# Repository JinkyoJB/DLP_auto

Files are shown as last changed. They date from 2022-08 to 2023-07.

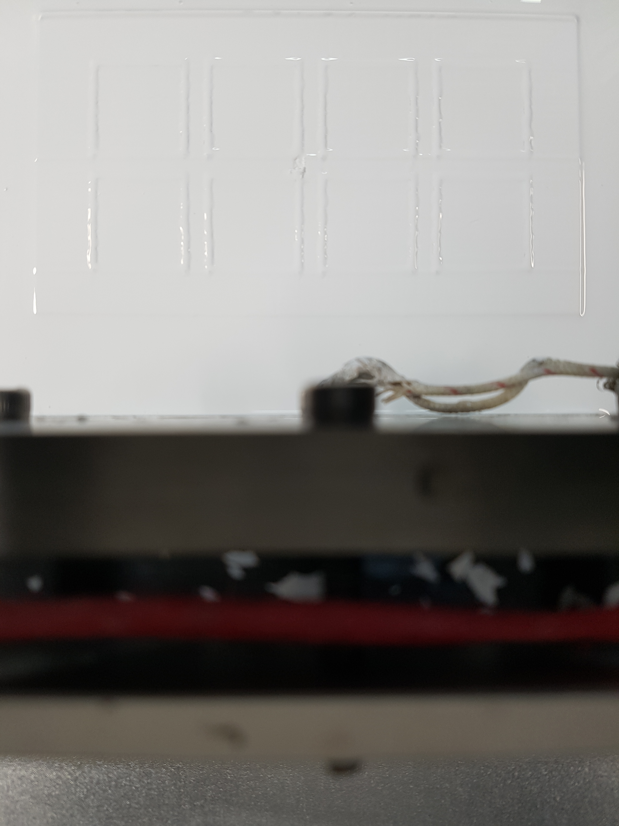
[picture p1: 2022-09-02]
DLP_GUI/DLP_temp/220808174041/20220629_163913.jpg

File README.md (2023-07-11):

# 딥러닝을 통한 DLP 3D프린터 출력 자동화

해당 내용은 서울과학기술대학교 특수정밀가공 및 생산연구실에서 진행하는 ‘ 세라믹 및 금속 재료의 3D 형상출력을 목적으로 제작된 광경화 타입 3D프린터 제작 및 딥러닝 기술을 기반으로 한 전공정 자동화 ’의 전반적인 기술 및 코드 내용입니다. 

https://user-images.githubusercontent.com/85150616/190361339-f62668f7-aa68-4073-84bd-3492f415d7a6.mp4

[제작된 3D프린터로 세라믹이 출력되는 모습]

## 1. Hardware

3D프린터의 하드웨어는 이전 연구실 연구원들이 제작한 세라믹용 광경화 3D프린터를 조금 더 개선시켜서 진행하였습니다. 자세한 규격 및 형상 정보는 ‘DLP_modeling’ 카테고리에 백업해 놓았습니다.

### 1.1. DLP_modeling

‘DLP_modeling’에서 [0.assembly-MLP_Original.prt](https://github.com/JinkyoJB/DLP_auto/blob/main/DLP_modeling/0.assembly-MLP_Original.prt) 항목은 개선시키기전 기존의 하드웨어의 데이터가 담겨있습니다. 파일형식은 ‘.prt’형식이며 NX Modeling 프로그램으로 제작되었습니다. 기존 DLP프린터 모습은 다음과 같습니다.

3D프린터-Original

[기존 3D프린터 모델링 데이터]

최종모델링
[최종 3D프린터 모델링 데이터]

[behind modeling]
  
고점도 세라믹 레진을 토출하기 위해 여러 모델링을 실험해 봤습니다.
<br>
1차적으로는 제어하기 쉬운 스텝모터를 이용해 여러 형상으로 토출을 시도해 봤으나 필요압력이 높아 구조물이 외압을 버티기 힘들어 3차 시도 끝에 공압기로 압력을 가해 토출하는 방식을 차용했습니다.

시료주사기

사용된 시료 주사기는 250ml 공업용 주사기에 3D프린터 및 o-ring으로 커스텀하여 사용하였습니다.

### 1.2. DLP_arduino
모터사양

아두이노는 시리얼 통신을 통해 말단의 모터,센서를 제어하며 컴퓨터의 GUI명령 또한 시리얼 통신으로 입력받습니다. 모터의 동작은 비동기방식이여야 하므로 일정 동작이 끝난 뒤, 아두이노는 '*'과 같은 특정 시그널을 통해 동작의 끝남을 컴퓨터에게 알리는 방식을 차용하였습니다.

### 1.3 블레이드 히팅

세라믹의 점도 및 흐름성은 온도에 반비례하는 특성을 지니므로 고점도 세라믹을 도포 시 40-70도의 블레이드가 필요합니다. 

따라서 모델링 및 가공하여 블레이드 양측에 열봉이 1개씩 삽입되고 중앙에 온도센서를 부착함으로써 히팅 블레이드를 적용했습니다.

### 1.4 flow-chart 및 diagram




---
## 2. Software

화면 캡처 2023-07-11 131624
3D프린터와 연결된 컴퓨터 화면에서는 위 이미지와 같은 화면을 볼 수 있습니다.
<br>


좌측 프로그램은 광원인 DLP 제어 프로그램이며, 중간은 3D프린터를 제어하기 위해 파이썬으로 자체 제작한 프로그램입니다. 해당 GUI를 통해 DLP에 input될 이미지, 광파워, 노광 시간, 3D프린터의 모터,센서를 조절할 수 있습니다. 또한 AI모드 출력 명령 버튼을 누르면 densenet을 적용하여 세라믹 표면에 결점이 발견 될 시 자동 재 블레이딩 및 블레이드 온도를 높이는 등의 폐루프 시스템을 적용할 수 있습니다.
맨 우측은 표면 결점을 검출하기 위해서 3D프린터 윗면에 달아둔 안드로이드기기를 통해 보여지는 이미지를 상시로 확인 할 수 있습니다. 안드로이드 연결은 파이썬을 이용해 ADB서버를 통해 통신합니다.

## 3. Deep learning

### 3.1. DLP_dataset
데이터셋은 2021.10.07~2022.02.23까지 실험 중 촬용된 세라믹 도표면 사진을 바탕으로 구성되었습니다.

정상상태(Normal)와 출력 중 빈번한 결함들로 분류했으며, 기계 자체적으로 조치를 취할 수 있는 상태인 미미한 결함(Minor defect)과 기공 상태(Pore), 적층이 아예 불가능한 심각한 상태(Critical) 및 기계오류 문제(Error) 로 총 5가지의 유형으로 분류했습니다.

### 3.2. DLP_data_augmentation
table2
데이터셋의 정확도를 높이기 위해 원본 이미지에 적절한 변형을 가해서 학습데이터셋의 규모를 인위적으로 증대하는 augmentation 기법을 적용했습니다. 각 분류의 데이터셋 양을 비슷하게 조절하고 각 가중치를 비슷하게 학습하여 정규화 및 과적합을 줄였으며, 종류는 기본적인 좌우반전, 상하반전, 랜덤위치합성 3가지를 적용했습니다. Augmentation을 적용한 최종 개수의 전체비율이 25%내외가 되도록 하여 가중치를 비슷하게 학습하도록 적용하였습니다.

이 외에도 세라믹 도표면은 광경화 반응이 일어 날 수 있도록 회백색인 경우가 많은데 이는 RGB의 값이 (255,255,255)로 편중되어 있음을 말합니다. 따라서 RGB픽셀값 표준화를 적용하여 주변 픽셀 대비 연산 픽셀의 RGB값의 변화가 더 쉽게 인식될 수 있도록 하여 학습 효율을 높였습니다. RGB평균값은 [0.485,0.456,0.406], 표준편차는 [0.229,0.224,0.225]를 적용하였으며, 적용된 최종 입력데이터의 이미지는 위 사진과 같습니다. 적용 후 보통 3%정도의 성능 향상을 확인했습니다.

### 3.3. DLP_deepLearning


준비된 데이터셋을 저명한 이미지 알고리즘에 파인 튜닝하여 적용해 본 결과, 어느정도 saturation된 결과값이 나온 것을 확인 할 수 있었습니다. 특히 denseNet에서 좋은 성능지표를 보여 해당 모델의 하이퍼파라미터를 optimization하여 3D프린터에 적용하였습니다.

---

### 결과

이렇게 폐루프 시스템으로 동작하는 세라믹 3D프린터의 출력 결과물입니다. 딥러닝을 통해 결함을 검출함으로써 sintered body에서도 정밀하고 적은 크랙을 관찰할 수 있었습니다.

### 3.4. DLP_yolo5(testing)
현재는 도포 과정이 아닌 전과정에서 일어날 수 있는 결함을 yolo5로 관측하기 위해 test 중입니다.

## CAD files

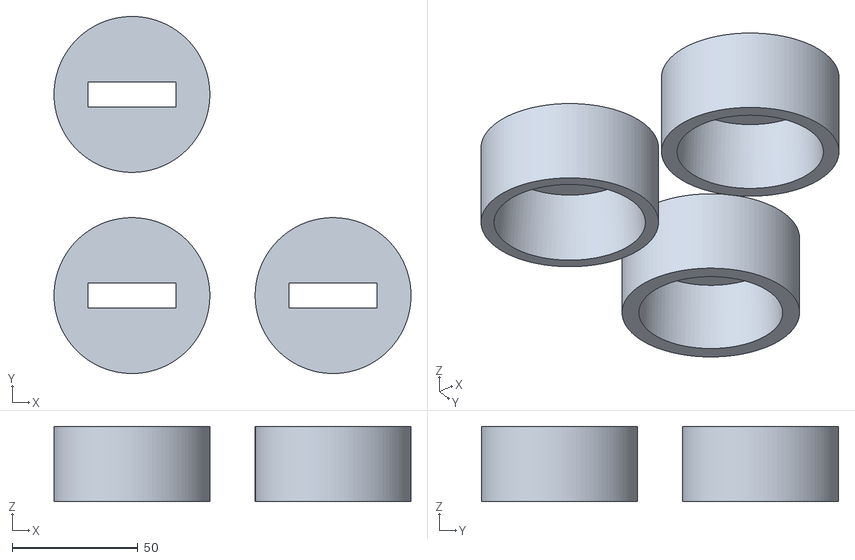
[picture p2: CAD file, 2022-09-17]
DLP_modeling/STL_files/0218_주둥이 마개.stl
142.0 x 142.0 x 30.0

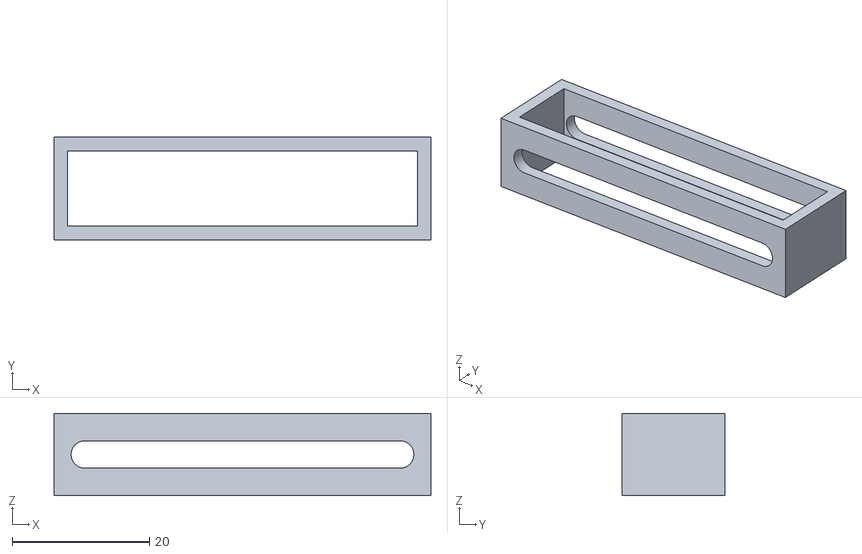
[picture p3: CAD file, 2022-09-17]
DLP_modeling/STL_files/z-limit 2.stl
55.0 x 15.0 x 12.0

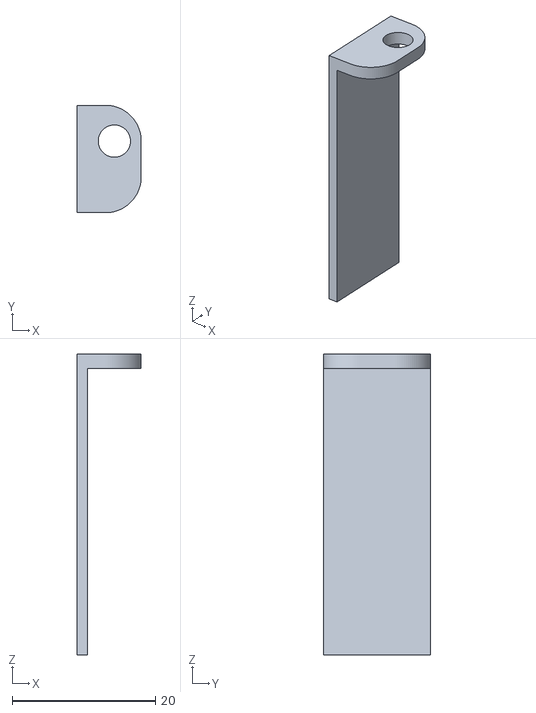
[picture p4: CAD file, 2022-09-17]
DLP_modeling/STL_files/z-limit 1.stl
9.00 x 15.0 x 42.0

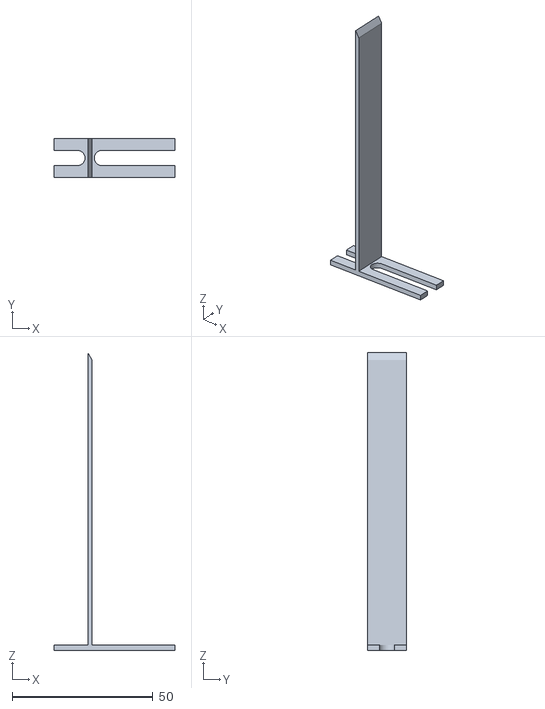
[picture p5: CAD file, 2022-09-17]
DLP_modeling/STL_files/b-limit 1.stl
43.0 x 14.0 x 106.0

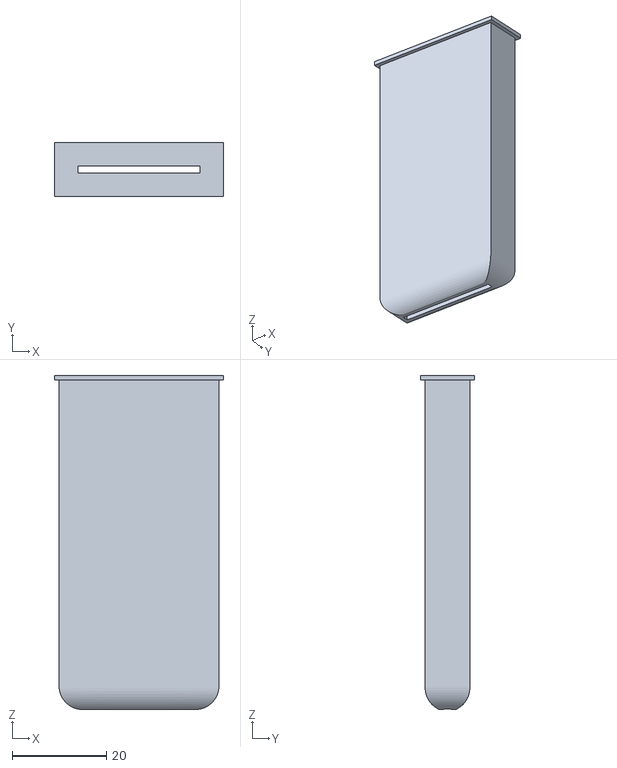
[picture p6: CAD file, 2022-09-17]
DLP_modeling/STL_files/0218_시료 주둥이.stl
36.0 x 11.5 x 71.0

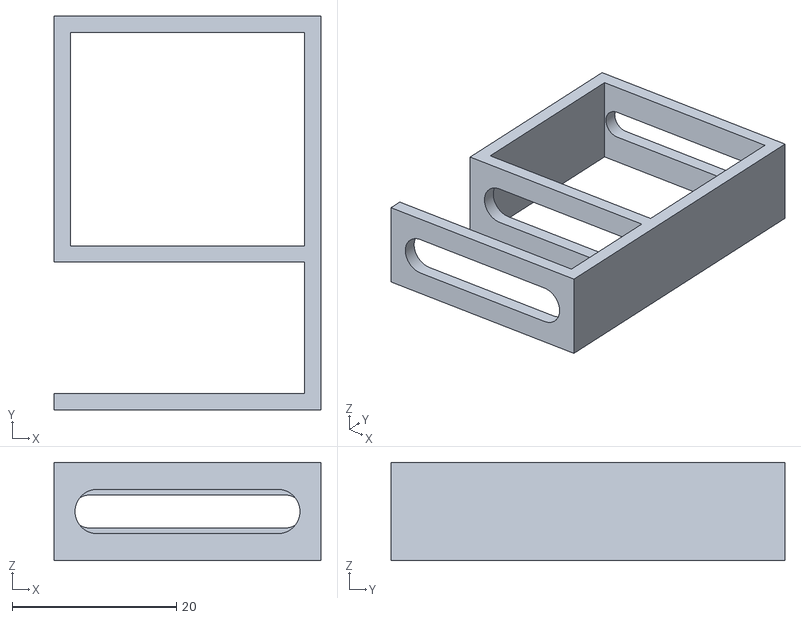
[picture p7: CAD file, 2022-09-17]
DLP_modeling/STL_files/b-limit 2.stl
32.5 x 48.0 x 12.0

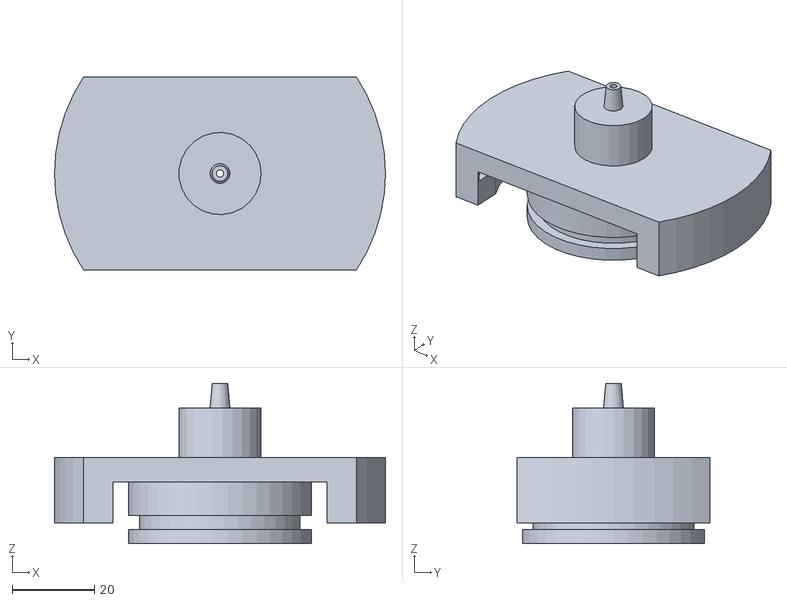
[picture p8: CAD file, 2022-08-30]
DLP_modeling/STL_files/27.air_hose.stl
80.5 x 47.0 x 39.0

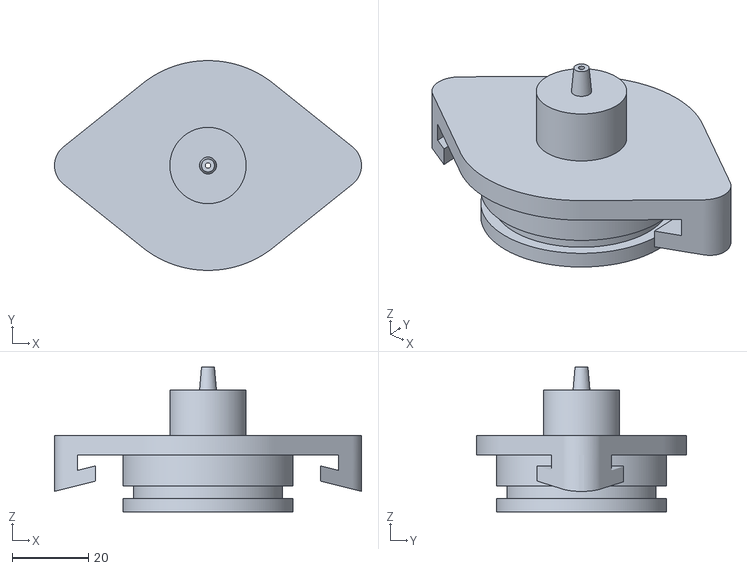
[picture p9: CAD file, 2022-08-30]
DLP_modeling/STL_files/air_hose(olde2).stl
80.5 x 55.0 x 38.0

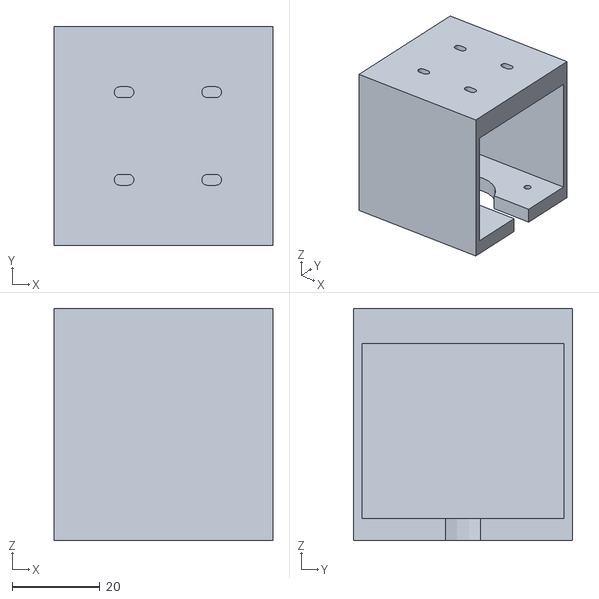
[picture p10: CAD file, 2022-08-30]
DLP_modeling/STL_files/motor-holder2.stl
50.0 x 50.0 x 53.0

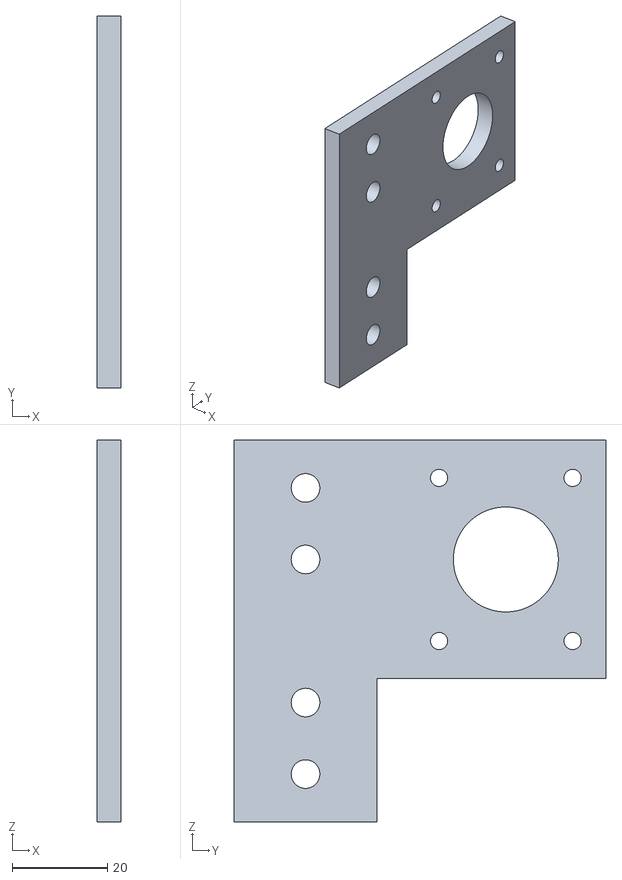
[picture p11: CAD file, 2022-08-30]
DLP_modeling/STL_files/33.motor_holer.stl
5.00 x 78.0 x 80.0

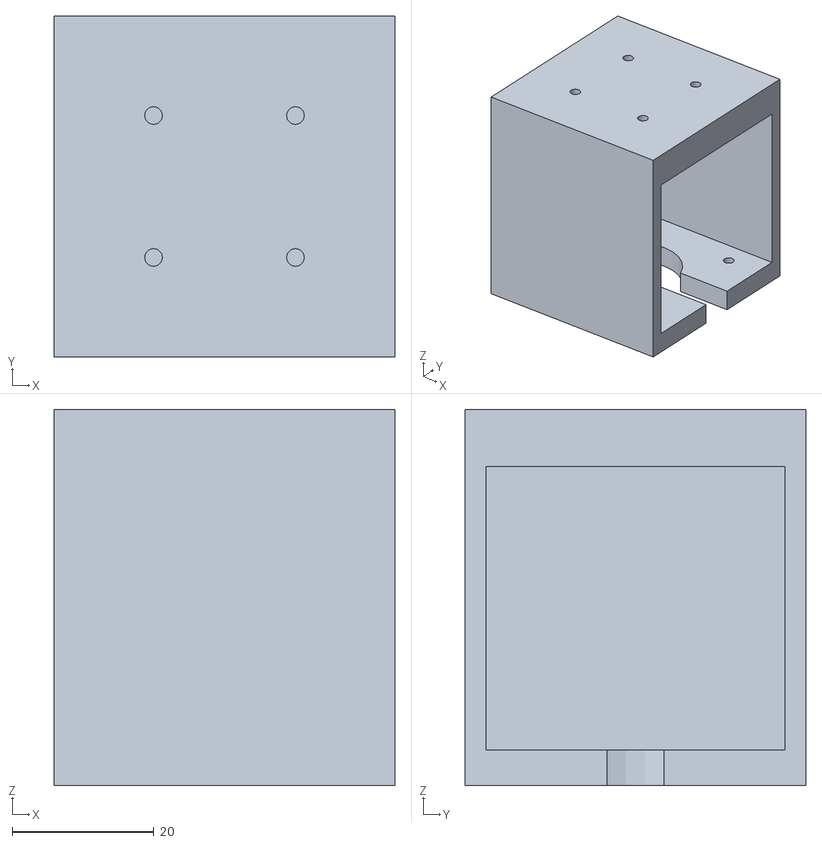
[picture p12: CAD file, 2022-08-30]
DLP_modeling/STL_files/motor-holder.stl
48.0 x 48.0 x 53.0

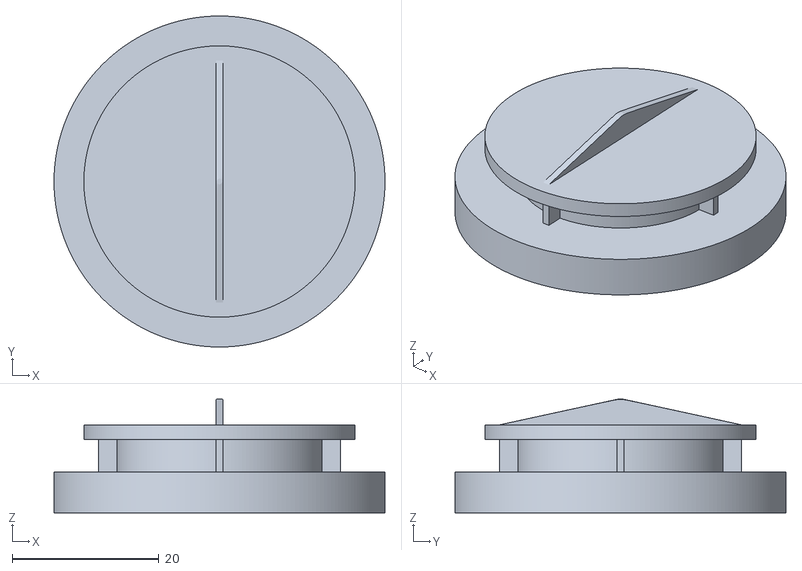
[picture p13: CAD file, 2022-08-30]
DLP_modeling/STL_files/air_cap.stl
45.2 x 45.2 x 15.5

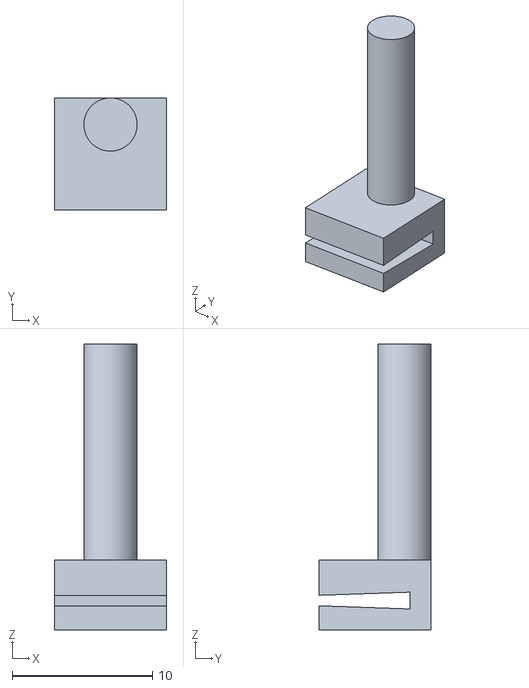
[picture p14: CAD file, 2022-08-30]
DLP_modeling/STL_files/cooling_pan_holder.stl
8.00 x 8.00 x 20.4

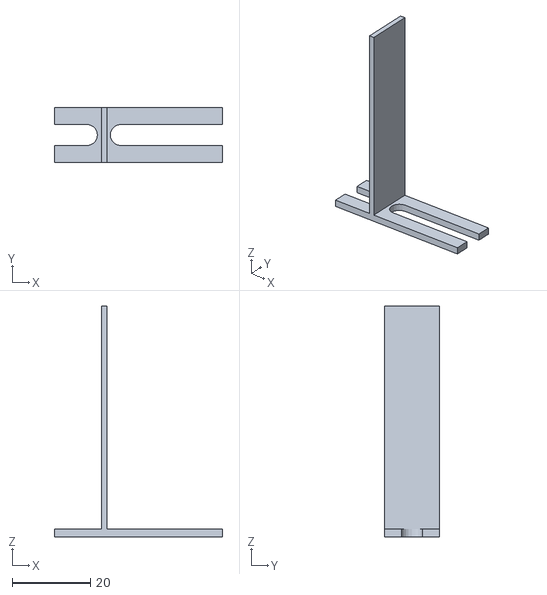
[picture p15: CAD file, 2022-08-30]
DLP_modeling/STL_files/210917 JS limitsensor-touch.stl
43.0 x 14.0 x 59.0

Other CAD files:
DLP_modeling/STL_files/211122-holder.stl
DLP_modeling/STL_files/211122-holder2.stl
DLP_modeling/STL_files/211026-2.stl
DLP_modeling/STL_files/air_hose(old).stl
DLP_modeling/0.assembly-MLP_Original.prt
DLP_modeling/00.assembly4-MLP_design.prt
DLP_modeling/1.Z-axis_frame.prt
DLP_modeling/10.ballscrew_of_gidebar.prt
DLP_modeling/11.Y_axis_acryle_part.prt
DLP_modeling/12.motor_bearing.prt
DLP_modeling/14.Y_axis_front_acrylic.prt
DLP_modeling/15.Y_axis_back_acrylic.prt
DLP_modeling/16.Y_axis_screw_bar_movement.prt
DLP_modeling/17.DLP.prt
DLP_modeling/18.Z-screw.prt
DLP_modeling/19.Z-axis_gide_bar.prt
DLP_modeling/2.X-axis_frame.prt
DLP_modeling/20.Z-axis_scew_movement..prt
DLP_modeling/21.blade_bar.prt
DLP_modeling/23.Y-axis_plate.prt
DLP_modeling/24.plate.prt
DLP_modeling/25.phone_plate.prt
DLP_modeling/27.air_hose_.prt
DLP_modeling/28.syringe_holer.prt
DLP_modeling/29.air_cap.prt
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

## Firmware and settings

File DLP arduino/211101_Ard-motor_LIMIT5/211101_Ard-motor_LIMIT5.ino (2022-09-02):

//제어용 아두이노 포트번호는 16 
//21.11.02 모터 드라이버 교체--> 이전버전 코드와 모터 방향 반대
//21.11.17 레진 모터 추가
#define Blade_DIR 53
#define Blade_STEP 51
#define Blade1_ms1 49
#define Blade1_ms2 47
#define Blade1_SP 45
#define Blade2_ms1 43
#define Blade2_ms2 41
#define Blade2_SP 39
#define Blade_e 37 //Enable

#define zaxis_DIR 52
#define zaxis_STEP 50
#define zaxis1_ms1 48
#define zaxis1_ms2 46
#define zaxis1_SP 44
#define zaxis2_ms1 42
#define zaxis2_ms2 40
#define zaxis2_SP 38
#define zaxis_e 30 //Enable

#define button 34 //0812업글
#define sensor 32 //0812업글

#define resin_SIG 2
#define Rsensor 3 
#define resin_e 4 //enable
#define resin_ms1 5
#define resin_ms2 6
#define resin_SP 7
#define resin_STEP 8
#define resin_DIR 9



void setup()
{
  pinMode(resin_e, OUTPUT);
  pinMode(Blade_e, OUTPUT);
  pinMode(zaxis_e, OUTPUT);
  digitalWrite(Blade_e,LOW);
  digitalWrite(zaxis_e,LOW);
  digitalWrite(resin_e,LOW);
  pinMode(Blade_DIR, OUTPUT);
  pinMode(Blade_STEP, OUTPUT);
  pinMode(Blade1_SP, OUTPUT);
  pinMode(Blade1_ms2, OUTPUT);
  pinMode(Blade1_ms1, OUTPUT);
  pinMode(Blade2_SP, OUTPUT);
  pinMode(Blade2_ms2, OUTPUT);
  pinMode(Blade2_ms1, OUTPUT);
 
  pinMode(resin_DIR, OUTPUT);
  pinMode(resin_STEP,OUTPUT);
  pinMode(resin_SP, OUTPUT);
  pinMode(resin_ms2, OUTPUT);
  pinMode(resin_ms1, OUTPUT);

  pinMode(zaxis_DIR, OUTPUT);
  pinMode(zaxis_STEP,OUTPUT);
  pinMode(zaxis1_SP, OUTPUT);
  pinMode(zaxis1_ms2, OUTPUT);
  pinMode(zaxis1_ms1, OUTPUT);
  pinMode(zaxis2_SP, OUTPUT);
  pinMode(zaxis2_ms2, OUTPUT);
  pinMode(zaxis2_ms1, OUTPUT);
  pinMode(resin_SIG, OUTPUT);
  
  pinMode(button, INPUT_PULLUP);
  pinMode(sensor, INPUT_PULLUP);
  pinMode(Rsensor, INPUT_PULLUP);
 
 Serial.begin(9600);
}
 
void loop()
{ 
  digitalWrite(resin_SIG,LOW);
  if(Serial.available() > 0)
  {
    String inString = Serial.readStringUntil('\n');
    int index1 = inString.indexOf(','); //문자열에 '찾을문자'가 있는 위치(index)값 반환
    int index2 = inString.indexOf(',', index1+1); //('찾을문자', 시작위치) 문자열의 시작위치에서 시작하고 '찾을문자'가 있는 위치값 반환
    int index3 = inString.length();
    int value1 = inString.substring(0, index1).toInt();
    int value2 = inString.substring(index1+1,index2).toInt();
    int value3 = inString.substring(index2+1,index3).toInt();
    
 ////Value2가 0이면 z축 관련
    if((value1 == 0) & (value2 == 0) & (value3 == 1)) /// z축이 리미트센서에 터치
    {
      zhoming();
    }
    if((value1 == 0) & (value2 == 0) & (value3 == 2)) /// z축이 블레이드 날에 닿는 위치로
    {
      zgoing();
    }

 ///value2 가 1이면 blade 관련
   if((value1 == 0) & (value2 == 1) & (value3 == 1)) ///blade Homing, 블레이드 시작 위치에서 멈추기
    {
      bhoming();
    }
   if((value1 == 0) & (value2 == 1) & (value3 == 2)) ///blade going
   {
      bgoing();
   }

   //resin함수
      if((value1 == 2) & (value2 == 2) & (value3 == 2))
   {
      resinshot();
   }
      if((value1 == 0) & (value2 == 0) & (value3 == 3)) 
    {
      Rhoming();
    }
      if((value1 == 4) & (value2 == 4) & (value3 == 4)) 
    {
      resinMS();
    }

 ///원하는 스텝만큼 모터이동하는 함수들
    if(value1 == 7) //7은 blade함수
    {
      Serial.print(" blade:"); Serial.print(value3); Serial.print("step");
      blade(value2, value3);
    }
    if(value1 == 8) //8은 zaxis함수 
    {
      Serial.print(" zaxis:"); Serial.print(value3); Serial.print("step");
      zaxis(value2, value3); 
    }
       if(value1 == 9) //9은 resin함수 
    {
      Serial.print(" resin:"); Serial.print(value3); Serial.print("step");
      resin(value2, value3); 
    }
  }
}

//blade 모터이동 2400step--6mm   1step당 0.0025mm
void blade(int direct, int step) // direct는 방향: 1은 앞으로, 0은 뒤로, step은 모터 step수,
{
    digitalWrite(Blade1_SP,LOW);
    digitalWrite(Blade1_ms2,HIGH);
    digitalWrite(Blade1_ms1,LOW);
    digitalWrite(Blade2_SP,LOW);
    digitalWrite(Blade2_ms2,HIGH);
    digitalWrite(Blade2_ms1,LOW);
  if(direct == 1)
  { 
    Serial.println(" forward");
    digitalWrite(Blade_DIR,LOW);
    for(int i = 0; i < step; i++)
      {
        digitalWrite(Blade_STEP,HIGH);
        delayMicroseconds(500);
        digitalWrite(Blade_STEP,LOW);
        delayMicroseconds(500);
      }
     Serial.println("*"); 
  }
  if(direct == 0)
  {
    Serial.println(" backward");
    digitalWrite(Blade_DIR,HIGH);
    for(int i = 0; i < step; i++)
      {
        digitalWrite(Blade_STEP,HIGH);
        delayMicroseconds(500);
        digitalWrite(Blade_STEP,LOW);
        delayMicroseconds(500);
      }
    Serial.println("*");
  }
}
//Z모터이동 3200step--4mm   1step당 0.00125mm
void zaxis(int direct, int step) // direct는 방향: 1은 앞으로, 0은 뒤로, step은 모터 step수,
{
    digitalWrite(zaxis1_SP,LOW);
    digitalWrite(zaxis1_ms2,HIGH);
    digitalWrite(zaxis1_ms1,LOW);
    digitalWrite(zaxis2_SP,LOW);
    digitalWrite(zaxis2_ms2, HIGH);
    digitalWrite(zaxis2_ms1, LOW);
  if(direct == 1)
  {
    Serial.println(" up");
    digitalWrite(zaxis_DIR,LOW);
    for(int i = 0; i < step; i++)
      {
        digitalWrite(zaxis_STEP,HIGH);
        delayMicroseconds(1000);
        digitalWrite(zaxis_STEP,LOW);
        delayMicroseconds(1000);
      }
    Serial.println("*");
  }
  if(direct == 0)
  {
    Serial.println(" down");
    digitalWrite(zaxis_DIR,HIGH);
    for(int i = 0; i < step; i++)
      {
        digitalWrite(zaxis_STEP,HIGH);
        delayMicroseconds(1000);
        digitalWrite(zaxis_STEP,LOW);
        delayMicroseconds(1000);
      }
    Serial.println("*");
  }
}
 
void bhoming()
{
  Serial.println(" homing-blade");
  digitalWrite(Blade1_SP,LOW);
  digitalWrite(Blade1_ms2,LOW);
  digitalWrite(Blade1_ms1,LOW);
  digitalWrite(Blade2_SP,LOW);
  digitalWrite(Blade2_ms2,LOW);
  digitalWrite(Blade2_ms1,LOW);
 
  digitalWrite(Blade_DIR, LOW);
  
  for(int i = 0; i < 9999999; i++ ) 
  {
    if( digitalRead(button) == HIGH) 
    {
      Serial.println(" blade touched");
      break;
    } 
    else 
    {
      digitalWrite(Blade_STEP,HIGH);
      delayMicroseconds(700);
      digitalWrite(Blade_STEP,LOW);
      delayMicroseconds(700);
    }
  }
 Serial.println("*");
}

///블레이드시작위치로 부터 일정 스텝만큼 뒤로 이동하는 함수
void bgoing()
{
    digitalWrite(Blade1_SP, LOW);
    digitalWrite(Blade1_ms2,HIGH);
    digitalWrite(Blade1_ms1,LOW);
    digitalWrite(Blade2_SP,LOW);
    digitalWrite(Blade2_ms2,HIGH);
    digitalWrite(Blade2_ms1,LOW);

    digitalWrite(Blade_DIR, HIGH);
    
  for(int i = 0; i < 32000; i++)
  {
    digitalWrite(Blade_STEP,HIGH);
    delayMicroseconds(500);
    digitalWrite(Blade_STEP,LOW);
    delayMicroseconds(500);
  }
  for(int i = 0; i < 7600; i++)
  {
    digitalWrite(Blade_STEP,HIGH);
    delayMicroseconds(500);
    digitalWrite(Blade_STEP,LOW);
    delayMicroseconds(500);
  }
 Serial.println("*");
}

///z축이 리미트센서에 닿도록 아래로 이동하는 함수
void zhoming()
{
  Serial.println(" homing-Z-axis");
  digitalWrite(zaxis1_SP, LOW);    
  digitalWrite(zaxis1_ms2, HIGH);
  digitalWrite(zaxis1_ms1, LOW);
  digitalWrite(zaxis2_SP, LOW);
  digitalWrite(zaxis2_ms2, HIGH);
  digitalWrite(zaxis2_ms1, LOW);   
 
  digitalWrite(zaxis_DIR, HIGH);
  
  for(int i = 0; i < 9999999; i++ ) 
  {
    if( digitalRead(sensor) == HIGH ) 
    {
      Serial.println(" z-axis sensor touched");
      break;
    } 
    else 
    {
      digitalWrite(zaxis_STEP,HIGH);
      delayMicroseconds(700);
      digitalWrite(zaxis_STEP,LOW);
      delayMicroseconds(700);
    }
  }
  Serial.println("*");
}

///z판이 블레이드 날에 닿도록 일정위치 이동하는 함수 , 25.5mm 이동
void zgoing()
{
  Serial.println(" going-Z-axis");
  digitalWrite(zaxis1_SP, LOW);    
  digitalWrite(zaxis1_ms2, HIGH);
  digitalWrite(zaxis1_ms1, LOW);
  digitalWrite(zaxis2_SP, LOW);
  digitalWrite(zaxis2_ms2, HIGH);
  digitalWrite(zaxis2_ms1, LOW);    
 
  digitalWrite(zaxis_DIR, LOW);
   
  for(int i = 0; i < 22850; i++)   //23000
  {
    digitalWrite(zaxis_STEP,HIGH);
    delayMicroseconds(700);
    digitalWrite(zaxis_STEP,LOW);
    delayMicroseconds(700);
  }
 Serial.println("*");
}

void resinshot()
{
    Serial.println(" resin shot");
    digitalWrite(resin_SIG, HIGH);
    delay(1000);
    pinMode(resin_SIG, OUTPUT);
    Serial.println("*");
}


void resinMS()
{
  Serial.println(" resin moving and shot");
  digitalWrite(resin_SP,LOW);
  digitalWrite(resin_ms2,LOW);
  digitalWrite(resin_ms1,LOW);
    
  digitalWrite(resin_DIR,HIGH);  //오른쪽이 원위치! 15센치(30000step) 왼쪽으로 가서 시료뿌릴 위치로 이동
  for(int i = 0; i < 30000; i++)
  {
    digitalWrite(resin_STEP,HIGH);
    delayMicroseconds(200);
    digitalWrite(resin_STEP,LOW);
    delayMicroseconds(200);
  }
  delay(1000);  //1초 딜레이
  digitalWrite(resin_SIG, HIGH); //시료주사시작
  digitalWrite(resin_DIR, LOW);  //시료 뿌리면서 우측으로 10CM(20000STEP)이동
  for(int i = 0; i < 20000; i++)
  {
    digitalWrite(resin_STEP,HIGH);
    delayMicroseconds(200);
    digitalWrite(resin_STEP,LOW);
    delayMicroseconds(200);
  }
  digitalWrite(resin_SIG, LOW); //시료주사끝
  for(int i = 0; i < 10000; i++)  //끝으로 1CM 10000STEP더이동
  {
    digitalWrite(resin_STEP,HIGH);
    delayMicroseconds(200);
    digitalWrite(resin_STEP,LOW);
    delayMicroseconds(200);
  }
  Serial.println("*");
}

///resin모터 이동 resin 800setp-->4mm  1step당 0.005mm
void resin(int direct, int step) // direct는 방향: 1은 앞으로, 0은 뒤로, step은 모터 step수
{
    digitalWrite(resin_SP,LOW);
    digitalWrite(resin_ms2,LOW);
    digitalWrite(resin_ms1,LOW);
  if(direct == 1)
  {
    Serial.println(" right");
    digitalWrite(resin_DIR,LOW);
    for(int i = 0; i < step; i++)
      {
        digitalWrite(resin_STEP,HIGH);
        delayMicroseconds(200);
        digitalWrite(resin_STEP,LOW);
        delayMicroseconds(200);
      }
    Serial.println("*");
  }
  if(direct == 0)
  {
    Serial.println(" left");
    digitalWrite(resin_DIR,HIGH);
    for(int i = 0; i < step; i++)
      {
        digitalWrite(resin_STEP,HIGH);
        delayMicroseconds(200);
        digitalWrite(resin_STEP,LOW);
        delayMicroseconds(200);
      }
    Serial.println("*");
  }
}

///Resin motor가리미트센서에 닿도록 아래로 이동하는 함수
void Rhoming()
{
  Serial.println(" homing-resin");
  digitalWrite(resin_SP,LOW);
  digitalWrite(resin_ms2,LOW);
  digitalWrite(resin_ms1,LOW);
 
  digitalWrite(resin_DIR, LOW);
  
  for(int i = 0; i < 9999999; i++ ) 
  {
    if( digitalRead(Rsensor) == LOW ) 
    {
      Serial.println(" resin sensor touched");
      break;
    } 
    else 
    {
      digitalWrite(resin_STEP,HIGH);
      delayMicroseconds(700);
      digitalWrite(resin_STEP,LOW);
      delayMicroseconds(700);
    }
  }
  Serial.println("*");
}

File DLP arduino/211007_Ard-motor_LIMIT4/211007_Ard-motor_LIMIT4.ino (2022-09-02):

//제어용 아두이노 포트번호는 16
#define Blade_DIR 53
#define Blade_STEP 51
#define Blade1_ms1 49
#define Blade1_ms2 47
#define Blade1_ms3 45
#define Blade2_ms1 43
#define Blade2_ms2 41
#define Blade2_ms3 39
#define Blade_e 37 //Enable
#define zaxis_DIR 52
#define zaxis_STEP 50
#define zaxis1_ms1 48
#define zaxis1_ms2 46
#define zaxis1_ms3 44
#define zaxis2_ms1 42
#define zaxis2_ms2 40
#define zaxis2_ms3 38
#define zaxis_e 30 //Enable

#define button 34 //0812업글
#define sensor 32 //0812업글
 
void setup()
{
  pinMode(Blade_e, OUTPUT);
  pinMode(zaxis_e, OUTPUT);
  digitalWrite(Blade_e,LOW);
  digitalWrite(zaxis_e,LOW);
  pinMode(Blade_DIR, OUTPUT);
  pinMode(Blade_STEP, OUTPUT);
  pinMode(Blade1_ms3, OUTPUT);
  pinMode(Blade1_ms2, OUTPUT);
  pinMode(Blade1_ms1, OUTPUT);
  pinMode(Blade2_ms3, OUTPUT);
  pinMode(Blade2_ms2, OUTPUT);
  pinMode(Blade2_ms1, OUTPUT);
 
  pinMode(zaxis_DIR, OUTPUT);
  pinMode(zaxis_STEP,OUTPUT);
  pinMode(zaxis1_ms3, OUTPUT);
  pinMode(zaxis1_ms2, OUTPUT);
  pinMode(zaxis1_ms1, OUTPUT);
  pinMode(zaxis2_ms3, OUTPUT);
  pinMode(zaxis2_ms2, OUTPUT);
  pinMode(zaxis2_ms1, OUTPUT);

  pinMode(button, INPUT_PULLUP);
  pinMode(sensor, INPUT_PULLUP);
 
 Serial.begin(9600);
}
 
void loop()
{  
  if(Serial.available() > 0)
  {
    String inString = Serial.readStringUntil('\n');
   
    int index1 = inString.indexOf(','); //문자열에 '찾을문자'가 있는 위치(index)값 반환
    int index2 = inString.indexOf(',', index1+1); //('찾을문자', 시작위치) 문자열의 시작위치에서 시작하고 '찾을문자'가 있는 위치값 반환
    int index3 = inString.length();
    int value1 = inString.substring(0, index1).toInt();
    int value2 = inString.substring(index1+1,index2).toInt();
    int value3 = inString.substring(index2+1,index3).toInt();

 ////Value2가 0이면 z축 관련
    if((value1 == 0) & (value2 == 0) & (value3 == 1)) /// z축이 리미트센서에 터치
    {
      zhoming();
    }
    if((value1 == 0) & (value2 == 0) & (value3 == 2)) /// z축이 블레이드 날에 닿는 위치로
    {
      zgoing();
    }

 ///value2 가 1이면 blade 관련
   if((value1 == 0) & (value2 == 1) & (value3 == 1)) ///blade Homing, 블레이드 시작 위치에서 멈추기
    {
      bhoming();
    }
   if((value1 == 0) & (value2 == 1) & (value3 == 2)) ///blade going
   {
      bgoing();
   }
   if((value1 == 1) & (value2 == 1) & (value3 == 1)) ///blade going
   {
      order();
   }

 ///원하는 스텝만큼 모터이동하는 함수들
    if(value1 == 7) //7은 blade함수 8은 zaxis함수 9는 piston함수
    {
      Serial.print("blade:"); Serial.print(value3); Serial.println("step");
      blade(value2, value3);
    }
    if(value1 == 8)
    {
      Serial.print("zaxis:"); Serial.print(value3); Serial.println("step");
      zaxis(value2, value3); 
    }
  }
}
 
void blade(int direct, int step) // direct는 방향: 1은 앞으로, 0은 뒤로, step은 모터 step수,
{
    digitalWrite(Blade1_ms3,HIGH);
    digitalWrite(Blade1_ms2,HIGH);
    digitalWrite(Blade1_ms1,HIGH);
    digitalWrite(Blade2_ms3,HIGH);
    digitalWrite(Blade2_ms2,HIGH);
    digitalWrite(Blade2_ms1,HIGH);
  if(direct == 1)
  {
    digitalWrite(Blade_DIR,HIGH);
    for(int i = 0; i < step; i++)
      {
        digitalWrite(Blade_STEP,HIGH);
        delayMicroseconds(1000);
        digitalWrite(Blade_STEP,LOW);
        delayMicroseconds(1000);
      }
  }
  if(direct == 0)
  {
    digitalWrite(Blade_DIR,LOW);
    for(int i = 0; i < step; i++)
      {
        digitalWrite(Blade_STEP,HIGH);
        delayMicroseconds(1000);
        digitalWrite(Blade_STEP,LOW);
        delayMicroseconds(1000);
      }
  }
}
 
void zaxis(int direct, int step) // direct는 방향: 1은 앞으로, 0은 뒤로, step은 모터 step수,
{
    digitalWrite(zaxis1_ms3,HIGH);
    digitalWrite(zaxis1_ms2,HIGH);
    digitalWrite(zaxis1_ms1,HIGH);
    digitalWrite(zaxis2_ms3,HIGH);
    digitalWrite(zaxis2_ms2, HIGH);
    digitalWrite(zaxis2_ms1, HIGH);
  if(direct == 1)
  {
    digitalWrite(zaxis_DIR,HIGH);
    for(int i = 0; i < step; i++)
      {
        digitalWrite(zaxis_STEP,HIGH);
        delayMicroseconds(1000);
        digitalWrite(zaxis_STEP,LOW);
        delayMicroseconds(1000);
      }
  }
  if(direct == 0)
  {
    digitalWrite(zaxis_DIR,LOW);
    for(int i = 0; i < step; i++)
      {
        digitalWrite(zaxis_STEP,HIGH);
        delayMicroseconds(1000);
        digitalWrite(zaxis_STEP,LOW);
        delayMicroseconds(1000);
      }
  }
}
 
void bhoming()
{
  Serial.println("homing-blade");
  digitalWrite(Blade1_ms3,LOW);
  digitalWrite(Blade1_ms2,LOW);
  digitalWrite(Blade1_ms1,LOW);
  digitalWrite(Blade2_ms3,LOW);
  digitalWrite(Blade2_ms2,LOW);
  digitalWrite(Blade2_ms1,LOW);
 
  digitalWrite(Blade_DIR, HIGH);
  
  for(int i = 0; i < 9999999; i++ ) 
  {
    if( digitalRead(button) == HIGH) 
    {
      Serial.println("blade touched");
      blade(0,0);
      break;
    } 
    else 
    {
      digitalWrite(Blade_STEP,HIGH);
      delayMicroseconds(1500);
      digitalWrite(Blade_STEP,LOW);
      delayMicroseconds(1500);
    }
  }
}

///블레이드시작위치로 부터 일정 스텝만큼 뒤로 이동하는 함수
void bgoing()
{
    digitalWrite(Blade1_ms3,HIGH);
    digitalWrite(Blade1_ms2,HIGH);
    digitalWrite(Blade1_ms1,HIGH);
    digitalWrite(Blade2_ms3,HIGH);
    digitalWrite(Blade2_ms2,HIGH);
    digitalWrite(Blade2_ms1,HIGH);

    digitalWrite(Blade_DIR, LOW);
    
  for(int i = 0; i < 20000; i++)
  {
    digitalWrite(Blade_STEP,HIGH);
    delayMicroseconds(500);0,0,
    digitalWrite(Blade_STEP,LOW);
    delayMicroseconds(500);
  }
    for(int i = 0; i < 18000; i++)
  {
    digitalWrite(Blade_STEP,HIGH);
    delayMicroseconds(500);
    digitalWrite(Blade_STEP,LOW);
    delayMicroseconds(500);
  }
}

///z축이 리미트센서에 닿도록 아래로 이동하는 함수
void zhoming()
{
  Serial.println("homing-Z-axis");
  digitalWrite(zaxis1_ms3, HIGH);    
  digitalWrite(zaxis1_ms2, HIGH);
  digitalWrite(zaxis1_ms1, HIGH);
  digitalWrite(zaxis2_ms3, HIGH);
  digitalWrite(zaxis2_ms2, HIGH);
  digitalWrite(zaxis2_ms1, HIGH);   
 
  digitalWrite(zaxis_DIR, LOW);
  
  for(int i = 0; i < 9999999; i++ ) 
  {
    if( digitalRead(sensor) == HIGH ) 
    {
      Serial.println("z-axis sensor touched");
      zaxis(0,0);
      break;
    } 
    else 
    {
      digitalWrite(zaxis_STEP,HIGH);
      delayMicroseconds(1000);
      digitalWrite(zaxis_STEP,LOW);
      delayMicroseconds(1000);
    }
  }
}

///z판이 블레이드 날에 닿도록 일정위치 이동하는 함수 , 25.5mm 이동
void zgoing()
{
  Serial.println("going-Z-axis");
  digitalWrite(zaxis1_ms3, HIGH);    
  digitalWrite(zaxis1_ms2, HIGH);
  digitalWrite(zaxis1_ms1, HIGH);
  digitalWrite(zaxis2_ms3, HIGH);
  digitalWrite(zaxis2_ms2, HIGH);
  digitalWrite(zaxis2_ms1, HIGH);    
 
  digitalWrite(zaxis_DIR, HIGH);
   
  for(int i = 0; i < 21700; i++)
  {
    digitalWrite(zaxis_STEP,HIGH);
    delayMicroseconds(1000);
    digitalWrite(zaxis_STEP,LOW);
    delayMicroseconds(1000);
  }
}

void order()
{
  zaxis(0, 3000);
  delay(15000);
  bhoming();
  zaxis(1, 2940);
  bgoing(); 
}

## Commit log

2021-11-05 Add files via upload
    ARDUINO
2021-11-19 Add files via upload
    211119 updated
    아두이노 1축 추가
2022-08-30 hardware) modeling_data_upload
    hardware_design
    [0.assembly-MLP_Original.prt, 00.assembly4-MLP_design.prt, 1.Z-axis_frame.prt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]
2022-08-30 Delete 211101_Ard-motor_LIMIT5 directory
    for update, delate
2022-08-30 DLP arduino_upload
    control) arduino_upload
2022-08-31 Delete DLP_data_augmentation/1) Image_Synthesis directory
    for capacity
2022-09-02 DLP_deepLearning) code upload
    [output.csv]
2022-09-02 arduino) older code upload for back-up
2022-09-17 modeling data update
    [0218_시료 주둥이.stl, 0218_주둥이 마개.stl, 27.air_hose_.prt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]
2022-09-17 modeling data
    [27.air_hose.prt]
